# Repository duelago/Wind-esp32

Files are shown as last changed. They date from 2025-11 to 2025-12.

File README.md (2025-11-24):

# WindFlag Color ESP32

vlcsnap-2025-11-21-15h04m04s446

WindFlag med "Windlight-funktionalitet". Bytt ut gamla esp8266 mot en esp32 med integrerad LCD-skärm i färg. Lådan är omodellerad för att passa den nya skärmen och är inte helt rund längre.

Windexpilen och pinne till pilen är identisk.
Skärmen lyser grön, röd eller blå beroende på om det är flygbart eller ej. Blå signalerar riktigt hård vind. 



Följande behövs för ett bygge:

<b>ESP32 med display (Enklast med versionen som kommer med headers fastlödda) :</b> https://www.waveshare.com/esp32-c6-lcd-1.47.htm
<br>
<b>Stepper Motor 28BYJ-48-5V och driver board ULN2003:</b> https://de.aliexpress.com/item/1005008207445943.html
<br>
<b>Hall sensor KY-003:</b> https://de.aliexpress.com/item/1005008528506743.html
<br>
<b>Dupont female-female 15 cm:</b> https://de.aliexpress.com/item/4000203371860.html
<br>
<b>Magnet 6x2 mm:</b> https://de.aliexpress.com/item/1005010052380726.html<br>
<b>USB-C-kabel med 90 graders böj</b> så att kabeln får plats i lådan. https://de.aliexpress.com/item/1005009685359407.html

Alla filer printas i PLA med 0.4 mm munstycke. Kör paint-on-support för öppningen till skärmen och välj snug support. Kompassrosen kräver ett färgbyte för de översta lagren. Printa windexpinnen i 45 graders lutning med support för att förbättra hållfastigheten.
<br>
Vi behöver ansluta två kablar till ground men har bara en ground-pinne så en splicad kabel behövs (enkelt att löda ihop) I övrigt behöver inget lödas om man köper esp32an med headers på plats från fabrik. 



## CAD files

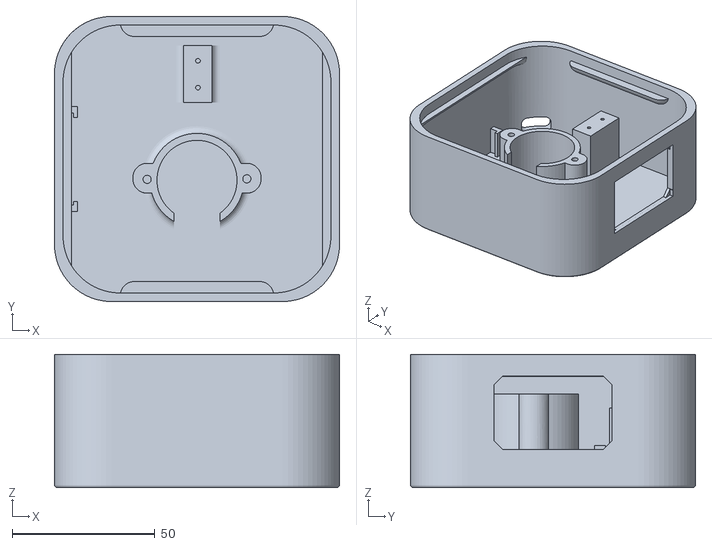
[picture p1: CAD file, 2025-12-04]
esp32-straight.stl
100.0 x 100.0 x 46.8

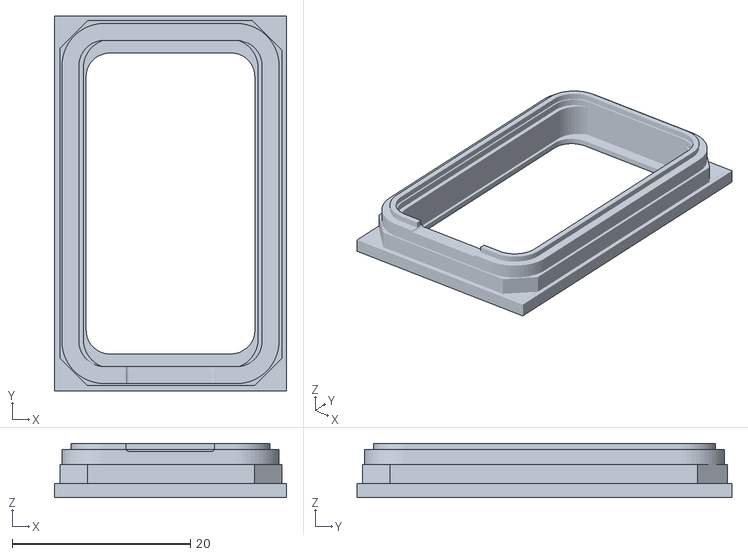
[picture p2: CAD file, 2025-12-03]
esp32-lcd-tpu-adapter.stl
26.0 x 42.0 x 6.11

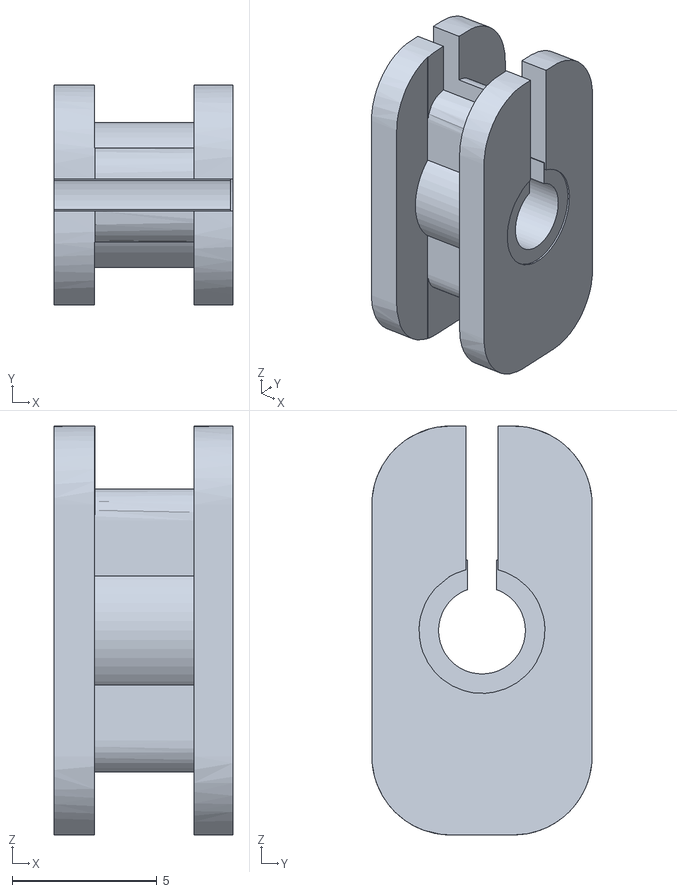
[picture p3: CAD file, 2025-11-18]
esp32-cable-holder-tpu.stl
6.18 x 7.62 x 14.2

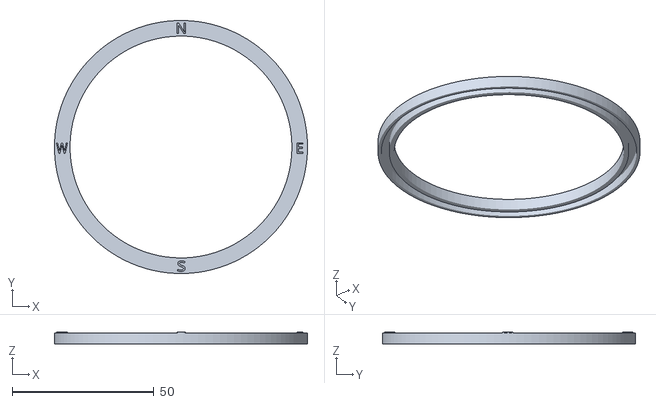
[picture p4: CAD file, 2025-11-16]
esp32-kompassros.stl
89.2 x 89.2 x 4.40

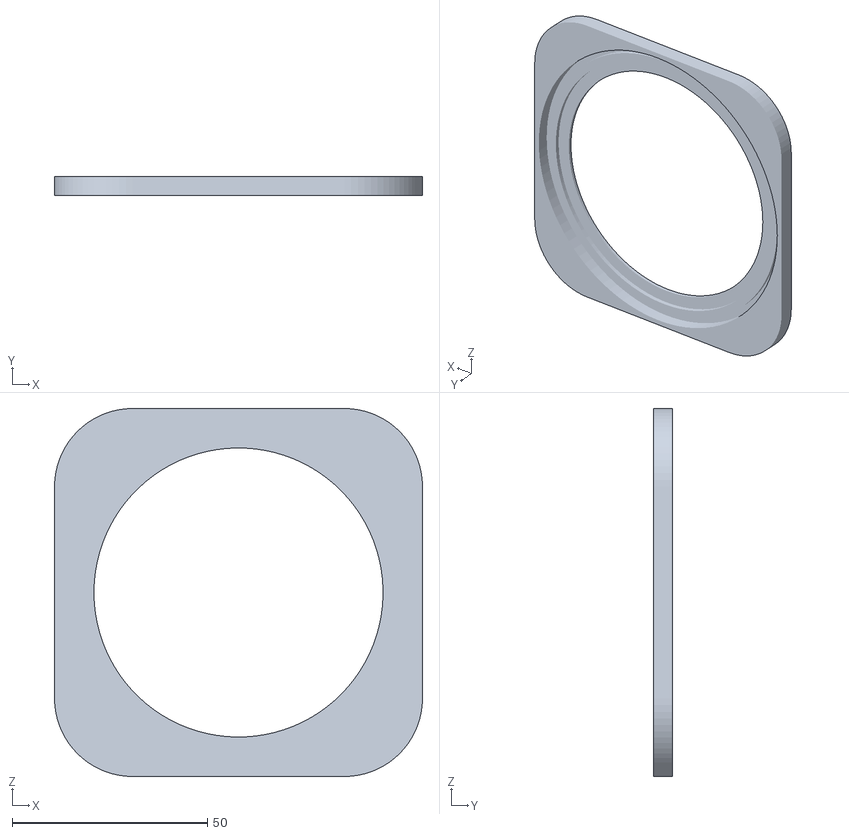
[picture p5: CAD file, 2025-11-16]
esp32-outer-lid-04.stl
94.2 x 4.80 x 94.2

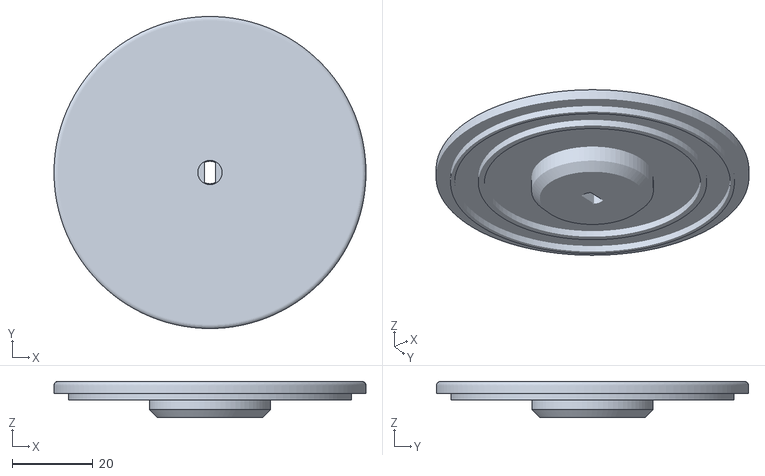
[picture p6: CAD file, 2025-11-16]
esp32-center-flagpole-lid.stl
77.2 x 77.2 x 9.00

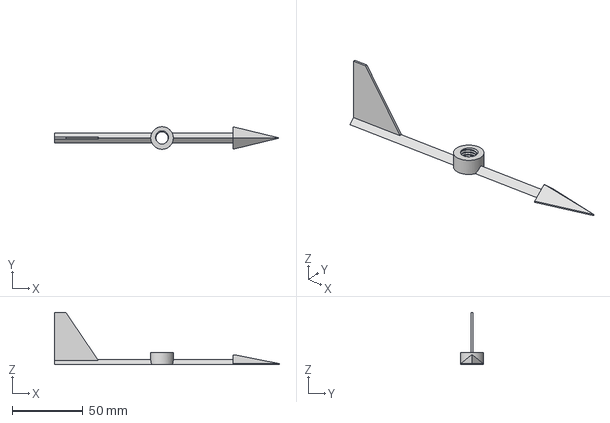
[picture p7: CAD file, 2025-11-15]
esp32-windex-pil.step
159.0 x 16.0 x 37.0 mm

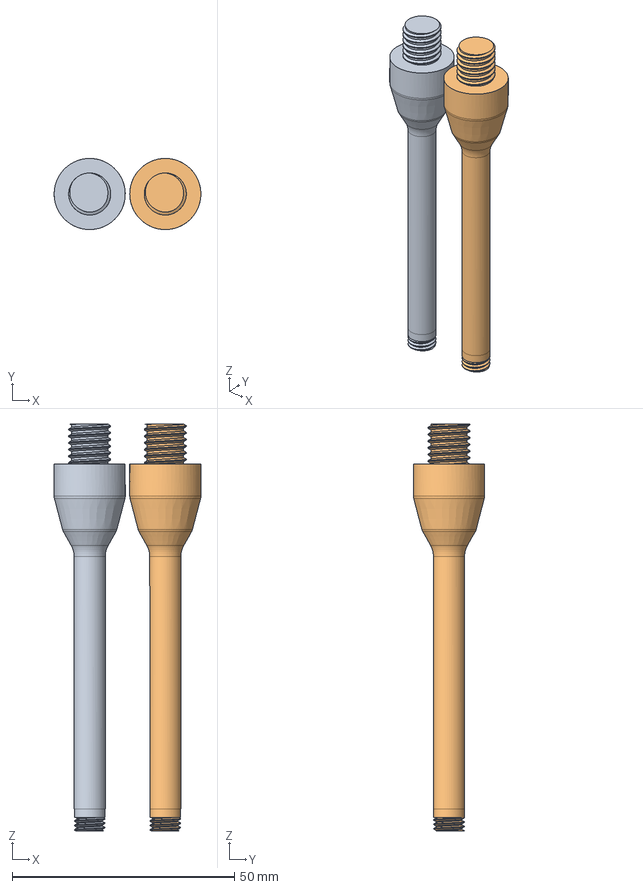
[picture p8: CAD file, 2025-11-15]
esp32-windex-pinnar.step
33.0 x 16.0 x 91.5 mm

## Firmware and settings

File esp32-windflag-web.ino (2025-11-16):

#include <WiFiManager.h>
#include <HTTPClient.h>
#include <ArduinoJson.h>
#include <FastLED.h>
#include <Arduino_GFX_Library.h>
#include <AccelStepper.h>
#include <SPI.h>
#include <EEPROM.h>
#include <WebServer.h>
#include <ESPmDNS.h>

#define LED_PIN 8
#define NUM_LEDS 1
CRGB leds[NUM_LEDS];

// ---------------- Display Configuration ----------------
#define TFT_CS   14
#define TFT_DC   15
#define TFT_RST  21
#define TFT_SCK  7
#define TFT_MOSI 6
#define TFT_BL   22

#define SCREEN_WIDTH 400
#define SCREEN_HEIGHT 320

Arduino_DataBus *bus = new Arduino_ESP32SPI(TFT_DC, TFT_CS, TFT_SCK, TFT_MOSI, -1);
Arduino_GFX *tft = new Arduino_ST7789(bus, TFT_RST, 1, true, SCREEN_WIDTH, SCREEN_HEIGHT);

#define MOTOR_PIN1 0
#define MOTOR_PIN2 1
#define MOTOR_PIN3 2
#define MOTOR_PIN4 3
#define HOME_SWITCH 18

// Motor parameters
#define STEPS_PER_ROTATION 4096
#define STEPPER_MAX_SPEED 400.0
#define STEPPER_HOMING_SPEED 100.0
#define STEPPER_ACC 100.0
#define STEPPER_HOMING_ACC 50.0

AccelStepper stepper(AccelStepper::HALF4WIRE, MOTOR_PIN1, MOTOR_PIN3, MOTOR_PIN2, MOTOR_PIN4, true);

// Calibration variables
long initHoming = -1;
int stepperCalibrationStep = 0;
bool homeSwitchInverse = true;
bool isCalibrated = false;

// Wind data structure
struct WindInfo {
    float speed;
    float direction;
    float temperature;
} windInfo;

// Debug flag
#define DEBUG true
#define DEBUG_SERIAL if (DEBUG) Serial

// Calibration flag - set to false to skip motor calibration
#define ENABLE_CALIBRATION true

// EEPROM addresses
#define HOLFUY_STATION_EEPROM_ADDRESS 0
#define HOLFUY_PASSWORD_EEPROM_ADDRESS 16
#define CONDITION_SETTINGS_ADDRESS 64
#define EEPROM_SIZE 512

// Holfuy configuration
String holfuy_station_id = "214";  // Default station
String holfuy_password = "correcthorsebatterystaple";  // Default password

// Condition settings structure
struct ConditionSettings {
    float green_min_speed;
    float green_max_speed;
    float green_min_direction;
    float green_max_direction;
    float blue_threshold;
} conditionSettings;

// Default condition settings
void setDefaultConditions() {
    conditionSettings.green_min_speed = 4.0;
    conditionSettings.green_max_speed = 8.0;
    conditionSettings.green_min_direction = 160.0;
    conditionSettings.green_max_direction = 260.0;
    conditionSettings.blue_threshold = 10.0;
}

// Web Server
WebServer server(80);

// Include FreeFonts
#include "Fonts/FreeSansBold24pt7b.h"
#include "Fonts/FreeSansBold18pt7b.h"

// EEPROM Functions
void writeStringToEEPROM(int addrOffset, const String &strToWrite) {
    byte len = strToWrite.length();
    EEPROM.write(addrOffset, len);
    for (int i = 0; i < len; i++) {
        EEPROM.write(addrOffset + 1 + i, strToWrite[i]);
    }
    EEPROM.commit();
    DEBUG_SERIAL.printf("[EEPROM] Wrote string to address %d: %s\n", addrOffset, strToWrite.c_str());
}

String readStringFromEEPROM(int addrOffset) {
    byte len = EEPROM.read(addrOffset);
    if (len == 0 || len == 255) {  // Empty or uninitialized
        return "";
    }
    char data[len + 1];
    for (int i = 0; i < len; i++) {
        data[i] = (char)EEPROM.read(addrOffset + 1 + i);
    }
    data[len] = '\0';
    String result = String(data).substring(0, len);
    DEBUG_SERIAL.printf("[EEPROM] Read string from address %d: %s\n", addrOffset, result.c_str());
    return result;
}

// Save condition settings to EEPROM
void saveConditionsToEEPROM() {
    EEPROM.put(CONDITION_SETTINGS_ADDRESS, conditionSettings);
    EEPROM.commit();
    DEBUG_SERIAL.println("[EEPROM] Condition settings saved");
}

// Load condition settings from EEPROM
void loadConditionsFromEEPROM() {
    ConditionSettings loaded;
    EEPROM.get(CONDITION_SETTINGS_ADDRESS, loaded);
    
    // Check if values are reasonable (not uninitialized EEPROM)
    if (loaded.green_min_speed >= 0 && loaded.green_min_speed < 100 &&
        loaded.green_max_speed > 0 && loaded.green_max_speed < 100 &&
        loaded.blue_threshold > 0 && loaded.blue_threshold < 100) {
        conditionSettings = loaded;
        DEBUG_SERIAL.println("[EEPROM] Condition settings loaded from EEPROM");
    } else {
        DEBUG_SERIAL.println("[EEPROM] No valid condition settings found, using defaults");
        setDefaultConditions();
        saveConditionsToEEPROM();
    }
    
    DEBUG_SERIAL.printf("[CONDITIONS] Green: %.1f-%.1f m/s, %.0f-%.0f degrees\n", 
                        conditionSettings.green_min_speed, conditionSettings.green_max_speed,
                        conditionSettings.green_min_direction, conditionSettings.green_max_direction);
    DEBUG_SERIAL.printf("[CONDITIONS] Blue threshold: %.1f m/s\n", conditionSettings.blue_threshold);
}

// Web Interface HTML
const char index_html[] PROGMEM = R"rawliteral(
<!DOCTYPE html>
<html lang="en">
<head>
<meta charset="utf-8">
<meta name="viewport" content="width=device-width, initial-scale=1">
<title>WindFlag - Configuration</title>
<style>
body {
    font-family: Arial, sans-serif;
    max-width: 800px;
    margin: 50px auto;
    padding: 20px;
    background-color: #f0f0f0;
}
.container {
    background-color: white;
    padding: 30px;
    border-radius: 10px;
    box-shadow: 0 2px 10px rgba(0,0,0,0.1);
}
h1 {
    color: #333;
    text-align: center;
}
h2 {
    color: #666;
    border-bottom: 2px solid #4CAF50;
    padding-bottom: 10px;
    margin-top: 30px;
}
.form-group {
    margin-bottom: 20px;
}
label {
    display: block;
    margin-bottom: 5px;
    font-weight: bold;
    color: #555;
}
input[type="text"], input[type="number"] {
    width: 100%;
    padding: 10px;
    border: 1px solid #ddd;
    border-radius: 5px;
    box-sizing: border-box;
    font-size: 16px;
}
input[type="submit"] {
    background-color: #4CAF50;
    color: white;
    padding: 12px 30px;
    border: none;
    border-radius: 5px;
    cursor: pointer;
    font-size: 16px;
    width: 100%;
    margin-top: 10px;
}
input[type="submit"]:hover {
    background-color: #45a049;
}
.current-config {
    background-color: #f9f9f9;
    padding: 15px;
    border-radius: 5px;
    margin-bottom: 20px;
    border-left: 4px solid #4CAF50;
}
.current-config p {
    margin: 5px 0;
    color: #666;
}
.condition-box {
    background-color: #f9f9f9;
    padding: 15px;
    border-radius: 5px;
    margin-bottom: 15px;
    border-left: 4px solid #ccc;
}
.condition-box.green { border-left-color: #4CAF50; }
.condition-box.blue { border-left-color: #2196F3; }
.condition-box.red { border-left-color: #f44336; }
.condition-box h3 {
    margin-top: 0;
    color: #333;
}
.form-row {
    display: grid;
    grid-template-columns: 1fr 1fr;
    gap: 15px;
}
.info-text {
    font-size: 14px;
    color: #666;
    font-style: italic;
    margin-top: 5px;
}
</style>
</head>
<body>
<div class="container">
<h1>💨 WindFlag Configuration</h1>

<div class="current-config">
<h3>Current Configuration</h3>
<p><strong>Station ID:</strong> %STATION_ID%</p>
<p><strong>Password:</strong> %PASSWORD_DISPLAY%</p>
<p><strong>IP Address:</strong> %IP_ADDRESS%</p>
</div>

<h2>Holfuy Station Settings</h2>
<form action="/saveholfuy" method="GET">
<div class="form-group">
<label for="station_id">Station ID:</label>
<input type="text" id="station_id" name="station_id" value="%STATION_ID%" required>
</div>
<div class="form-group">
<label for="password">Password:</label>
<input type="text" id="password" name="password" value="%PASSWORD%" required>
</div>
<input type="submit" value="Save Station Configuration">
</form>

<h2>Display Color</h2>
<form action="/saveconditions" method="GET">

<div class="condition-box green">
<h3>🟢 GREEN Condition (Good Wind)</h3>
<div class="form-row">
<div class="form-group">
<label for="green_min_speed">Min Speed (m/s):</label>
<input type="number" step="0.1" id="green_min_speed" name="green_min_speed" value="%GREEN_MIN_SPEED%" required>
</div>
<div class="form-group">
<label for="green_max_speed">Max Speed (m/s):</label>
<input type="number" step="0.1" id="green_max_speed" name="green_max_speed" value="%GREEN_MAX_SPEED%" required>
</div>
</div>
<div class="form-row">
<div class="form-group">
<label for="green_min_dir">Min Direction (degrees):</label>
<input type="number" step="1" id="green_min_dir" name="green_min_dir" value="%GREEN_MIN_DIRECTION%" required>
</div>
<div class="form-group">
<label for="green_max_dir">Max Direction (degrees):</label>
<input type="number" step="1" id="green_max_dir" name="green_max_dir" value="%GREEN_MAX_DIRECTION%" required>
</div>
</div>
<p class="info-text">Green indicates ideal wind conditions within specified speed and direction ranges</p>
</div>

<div class="condition-box blue">
<h3>🔵 BLUE Condition (High Wind)</h3>
<div class="form-group">
<label for="blue_threshold">Wind Speed Threshold (m/s):</label>
<input type="number" step="0.1" id="blue_threshold" name="blue_threshold" value="%BLUE_THRESHOLD%" required>
<p class="info-text">Blue indicates wind speed above this threshold (regardless of direction)</p>
</div>
</div>

<div class="condition-box red">
<h3>🔴 RED Condition (Poor Wind)</h3>
<p class="info-text">Red indicates all other conditions (wind outside green parameters and below blue threshold)</p>
</div>

<input type="submit" value="Save Condition Settings">
</form>

<div style="margin-top: 30px; text-align: center; color: #999; font-size: 12px;">
<p>WindFlag v2.1 - All settings saved to EEPROM</p>
<p>Contact info@holfuy.hu for station API credentials</p>
</div>
</div>
</body>
</html>
)rawliteral";

// Success page HTML
const char success_html[] PROGMEM = R"rawliteral(
<!DOCTYPE html>
<html lang="en">
<head>
<meta charset="utf-8">
<meta name="viewport" content="width=device-width, initial-scale=1">
<meta http-equiv="refresh" content="3;url=/">
<title>Configuration Saved</title>
<style>
body {
    font-family: Arial, sans-serif;
    max-width: 600px;
    margin: 50px auto;
    padding: 20px;
    background-color: #f0f0f0;
}
.container {
    background-color: white;
    padding: 30px;
    border-radius: 10px;
    box-shadow: 0 2px 10px rgba(0,0,0,0.1);
    text-align: center;
}
.success {
    color: #155724;
    font-size: 24px;
    margin-bottom: 20px;
}
</style>
</head>
<body>
<div class="container">
<div class="success">✅ Configuration Saved Successfully!</div>
<p>Station ID: <strong>%STATION_ID%</strong></p>
<p>Password: <strong>%PASSWORD_DISPLAY%</strong></p>
<p>Redirecting to main page in 3 seconds...</p>
<p><a href="/">Click here if not redirected</a></p>
</div>
</body>
</html>
)rawliteral";

// Handle root page
void handleRoot() {
    DEBUG_SERIAL.println("[WEB] Serving root page");
    String html = String(index_html);
    
    // Replace condition settings with longer placeholder names
    html.replace("%GREEN_MIN_SPEED%", String(conditionSettings.green_min_speed, 1));
    html.replace("%GREEN_MAX_SPEED%", String(conditionSettings.green_max_speed, 1));
    html.replace("%GREEN_MIN_DIRECTION%", String(conditionSettings.green_min_direction, 0));
    html.replace("%GREEN_MAX_DIRECTION%", String(conditionSettings.green_max_direction, 0));
    html.replace("%BLUE_THRESHOLD%", String(conditionSettings.blue_threshold, 1));
    
    // Then replace station settings
    html.replace("%STATION_ID%", holfuy_station_id);
    html.replace("%PASSWORD%", holfuy_password);
    html.replace("%PASSWORD_DISPLAY%", "********");
    html.replace("%IP_ADDRESS%", WiFi.localIP().toString());
    
    DEBUG_SERIAL.println("[WEB] Sending page with values:");
    DEBUG_SERIAL.printf("  Green min dir: %.0f\n", conditionSettings.green_min_direction);
    DEBUG_SERIAL.printf("  Green max dir: %.0f\n", conditionSettings.green_max_direction);
    
    server.send(200, "text/html", html);
}

// Handle save configuration
void handleSaveHolfuy() {
    DEBUG_SERIAL.println("[WEB] Saving Holfuy configuration");
    
    if (server.hasArg("station_id") && server.hasArg("password")) {
        holfuy_station_id = server.arg("station_id");
        holfuy_password = server.arg("password");
        
        DEBUG_SERIAL.printf("[WEB] New Station ID: %s\n", holfuy_station_id.c_str());
        DEBUG_SERIAL.printf("[WEB] New Password: %s\n", holfuy_password.c_str());
        
        // Save to EEPROM
        writeStringToEEPROM(HOLFUY_STATION_EEPROM_ADDRESS, holfuy_station_id);
        writeStringToEEPROM(HOLFUY_PASSWORD_EEPROM_ADDRESS, holfuy_password);
        
        // Send success page
        String html = String(success_html);
        html.replace("%STATION_ID%", holfuy_station_id);
        html.replace("%PASSWORD_DISPLAY%", "********");
        
        server.send(200, "text/html", html);
        
        DEBUG_SERIAL.println("[WEB] Configuration saved to EEPROM");
    } else {
        server.send(400, "text/plain", "Missing parameters");
        DEBUG_SERIAL.println("[WEB] Error: Missing parameters");
    }
}

// Handle save conditions
void handleSaveConditions() {
    DEBUG_SERIAL.println("[WEB] Saving condition settings");
    
    if (server.hasArg("green_min_speed") && server.hasArg("green_max_speed") &&
        server.hasArg("green_min_dir") && server.hasArg("green_max_dir") &&
        server.hasArg("blue_threshold")) {
        
        conditionSettings.green_min_speed = server.arg("green_min_speed").toFloat();
        conditionSettings.green_max_speed = server.arg("green_max_speed").toFloat();
        conditionSettings.green_min_direction = server.arg("green_min_dir").toFloat();
        conditionSettings.green_max_direction = server.arg("green_max_dir").toFloat();
        conditionSettings.blue_threshold = server.arg("blue_threshold").toFloat();
        
        DEBUG_SERIAL.println("[WEB] New Condition Settings:");
        DEBUG_SERIAL.printf("  Green: %.1f-%.1f m/s, %.0f-%.0f degrees\n", 
                           conditionSettings.green_min_speed, conditionSettings.green_max_speed,
                           conditionSettings.green_min_direction, conditionSettings.green_max_direction);
        DEBUG_SERIAL.printf("  Blue threshold: %.1f m/s\n", conditionSettings.blue_threshold);
        
        // Save to EEPROM
        saveConditionsToEEPROM();
        
        // Send success page
        String html = String(success_html);
        html.replace("%STATION_ID%", "Condition Settings");
        html.replace("%PASSWORD_DISPLAY%", "Updated Successfully");
        
        server.send(200, "text/html", html);
        
        DEBUG_SERIAL.println("[WEB] Condition settings saved to EEPROM");
    } else {
        server.send(400, "text/plain", "Missing parameters");
        DEBUG_SERIAL.println("[WEB] Error: Missing parameters");
    }
}

// Build API URL with current configuration
String getApiUrl() {
    String url = "https://api.holfuy.com/live/?s=" + holfuy_station_id + 
                 "&pw=" + holfuy_password + 
                 "&m=JSON&tu=C&su=m/s";
    return url;
}

// Function to calculate shortest distance for stepper rotation
static long shortest_distance(long origin, long target) {
    auto signedDiff = 0l;
    auto raw_diff = origin > target ? origin - target : target - origin;
    auto mod_diff = ((raw_diff % STEPS_PER_ROTATION) + STEPS_PER_ROTATION) % STEPS_PER_ROTATION;

    if (mod_diff > (STEPS_PER_ROTATION / 2)) {
        signedDiff = STEPS_PER_ROTATION - mod_diff;
        if (target > origin)
            signedDiff = -signedDiff;
    } else {
        signedDiff = mod_diff;
        if (origin > target)
            signedDiff = -signedDiff;
    }
    DEBUG_SERIAL.printf("[STEPPER] Shortest distance from %ld to %ld = %ld steps\n", origin, target, signedDiff);
    return signedDiff;
}

// Function to run stepper motor
void runStepper(long steps) {
    if (steps != 0) {
        DEBUG_SERIAL.printf("[STEPPER] Moving %ld steps\n", steps);
        stepper.enableOutputs();
        stepper.move(steps);
        stepper.runToPosition();
        delay(2);
        stepper.disableOutputs();
        DEBUG_SERIAL.println("[STEPPER] Movement complete");
    } else {
        DEBUG_SERIAL.println("[STEPPER] No movement needed (0 steps)");
    }
}

// Stepper calibration/homing routine (non-blocking)
bool stepperPosCalibrate() {
    pinMode(HOME_SWITCH, INPUT);

    switch (stepperCalibrationStep) {
        case 0:
            DEBUG_SERIAL.println("[CALIBRATION] Step 0: Starting homing sequence");
            stepper.stop();
            stepper.setMaxSpeed(STEPPER_MAX_SPEED);
            stepper.setAcceleration(STEPPER_ACC);
            stepper.enableOutputs();
            DEBUG_SERIAL.println("[CALIBRATION] Stepper is Homing...");
            stepperCalibrationStep = 10;
            break;
            
        case 10:
            stepper.move(initHoming);
            initHoming--;
            stepper.run();
            delay(5);
            if ((digitalRead(HOME_SWITCH) == LOW && !homeSwitchInverse) || 
                (digitalRead(HOME_SWITCH) == HIGH && homeSwitchInverse)) {
                DEBUG_SERIAL.println("[CALIBRATION] Step 10: Home switch triggered");
                stepperCalibrationStep = 20;
            }
            break;
            
        case 20:
            DEBUG_SERIAL.println("[CALIBRATION] Step 20: Setting zero position");
            stepper.setCurrentPosition(0);
            stepper.setMaxSpeed(STEPPER_HOMING_SPEED);
            stepper.setAcceleration(STEPPER_HOMING_ACC);
            initHoming = 1;
            stepperCalibrationStep = 30;
            break;
            
        case 30:
            stepper.move(initHoming);
            stepper.run();
            initHoming++;
            delay(5);
            if ((digitalRead(HOME_SWITCH) == HIGH && !homeSwitchInverse) || 
                (digitalRead(HOME_SWITCH) == LOW && homeSwitchInverse)) {
                DEBUG_SERIAL.println("[CALIBRATION] Step 30: Home switch released");
                stepperCalibrationStep = 40;
            }
            break;
            
        case 40:
            stepper.setCurrentPosition(0);
            DEBUG_SERIAL.println("[CALIBRATION] Step 40: Homing Completed Successfully");
            stepper.setMaxSpeed(STEPPER_MAX_SPEED);
            stepper.setAcceleration(STEPPER_ACC);
            stepper.disableOutputs();
            initHoming = -1;
            stepperCalibrationStep = 0;
            return true;
            
        default:
            break;
    }
    return false;
}

// Move stepper to wind direction (0-360 degrees)
void moveStepperToDirection(float targetDirection) {
    DEBUG_SERIAL.printf("[STEPPER] Moving to wind direction: %.1f degrees\n", targetDirection);
    auto targetPosition = long(targetDirection * double(STEPS_PER_ROTATION) / 360.0);
    auto currentPosition = stepper.currentPosition();
    DEBUG_SERIAL.printf("[STEPPER] Current position: %ld, Target position: %ld\n", currentPosition, targetPosition);
    runStepper(shortest_distance(currentPosition, targetPosition));
}

// Function to fetch data from the API
String fetchData(const char* apiUrl) {
    DEBUG_SERIAL.println("[HTTP] Starting API request...");
    DEBUG_SERIAL.printf("[HTTP] URL: %s\n", apiUrl);
    
    HTTPClient http;
    http.begin(apiUrl);
    http.setTimeout(10000);
    
    int httpCode = http.GET();
    DEBUG_SERIAL.printf("[HTTP] Response code: %d\n", httpCode);
    
    if (httpCode > 0) {
        String payload = http.getString();
        DEBUG_SERIAL.printf("[HTTP] Response length: %d bytes\n", payload.length());
        DEBUG_SERIAL.println("[HTTP] Response data:");
        DEBUG_SERIAL.println(payload);
        http.end();
        return payload;
    } else {
        DEBUG_SERIAL.printf("[HTTP] Error: %s\n", http.errorToString(httpCode).c_str());
        http.end();
        return "";
    }
}

// Function to display centered wind speed
void displayCenteredWindSpeed(float speed, uint16_t textColor, uint16_t bgColor) {
    DEBUG_SERIAL.printf("[DISPLAY] Updating display - Speed: %.1f m/s\n", speed);
    tft->fillScreen(bgColor);
    
    char speedStr[8];
    dtostrf(speed, 0, 1, speedStr);
    
    tft->setFont(&FreeSansBold24pt7b);
    tft->setTextColor(textColor);
    
    int16_t x1, y1;
    uint16_t w_speed, h_speed;
    tft->getTextBounds(speedStr, 0, 0, &x1, &y1, &w_speed, &h_speed);
    
    int startX = (SCREEN_WIDTH - w_speed) / 2;
    int yPos = (SCREEN_HEIGHT / 2);
    
    tft->setCursor(startX, yPos);
    tft->print(speedStr);
    
    DEBUG_SERIAL.println("[DISPLAY] Display update complete");
}
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
void loop() {
    static unsigned long loopCount = 0;
    static unsigned long lastUpdate = 0;
    unsigned long currentMillis = millis();
    
    // Handle web server requests
    server.handleClient();
    
    // Update weather data every 60 seconds
    if (currentMillis - lastUpdate >= 60000 || lastUpdate == 0) {
        lastUpdate = currentMillis;
        loopCount++;
        
        DEBUG_SERIAL.println("\n---------------------------------");
        DEBUG_SERIAL.printf("Loop iteration: %lu\n", loopCount);
        DEBUG_SERIAL.printf("Free heap: %d bytes\n", ESP.getFreeHeap());
        DEBUG_SERIAL.println("---------------------------------");
        
        if (WiFi.status() == WL_CONNECTED) {
            DEBUG_SERIAL.println("[WIFI] WiFi connected, fetching data...");
            String apiUrl = getApiUrl();
            String jsonResponse = fetchData(apiUrl.c_str());
            if (jsonResponse.length() > 0) {
                processJSON(jsonResponse);
            } else {
                DEBUG_SERIAL.println("[ERROR] Empty response from API");
            }
        } else {
            DEBUG_SERIAL.println("[ERROR] WiFi not connected. Reconnecting...");
            tft->fillScreen(BLACK);
            tft->setCursor(20, 80);
            tft->setTextSize(2);
            tft->println("WiFi Error!");
            WiFi.reconnect();
        }
    }
    
    delay(10); // Small delay to prevent watchdog issues
}

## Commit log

2025-11-16 Update esp32-windflag-web.ino
    Working :)
2025-11-18 Add files via upload
    Printa i TPU
    [esp32-cable-holder-tpu.stl]
2025-11-23 Update esp32-luftikus.ino
    km/h added
2025-12-03 Add files via upload
    Used to get a softer attachment of the sensitive LCD screen
    [esp32-lcd-tpu-adapter.stl]
2025-12-03 Add files via upload
    New version. Use with the TPU adapter
    [esp32-straight.stl]
